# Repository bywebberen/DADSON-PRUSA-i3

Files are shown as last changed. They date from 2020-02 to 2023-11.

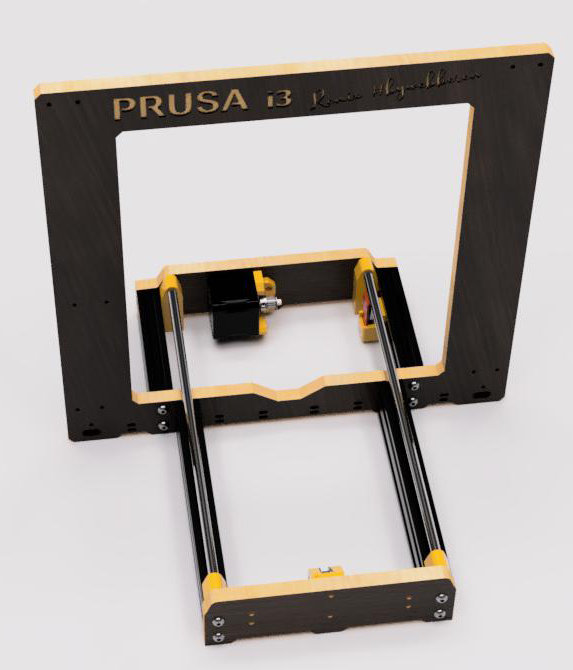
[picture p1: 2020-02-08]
IMGs/DADSON_Prusa_i3_printer_Y_AXIS.jpg

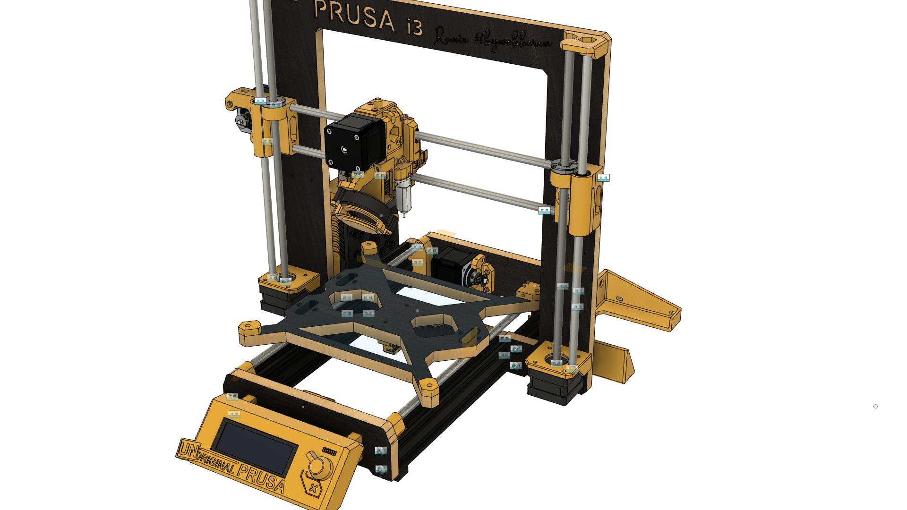
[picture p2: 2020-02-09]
IMGs/DADSON Prusa i3 printer v220.jpg

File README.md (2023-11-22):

# DADSON-PRUSA-i3
Another clone of the amazing PRUSA i3 3D-Printer by Josef Prusa

If you found this useful, please donate what you think it is worth to my paypal.me. Help cover the time of design.
Thanks, Enjoy!
http://www.paypal.me/bywebberen

Update 22.11.2023 - Added in an extruder assembly for the X1C bambulab hotend clone or real (remember this heater is running 24 volt)

Update 10.09.2020 — The Clip-on piece was actually uploaded...! Find it in X-axis folder named: "Homing_Block_sensorless homing.stl"

Update 29.08.2020 — There is a new motor piece for the X-axis part, if you haven't already printed it?
I will make a clipon piece today, which will  work the same. It is for when homing, if you are above the stability piece on the Z-axis, you will get 2 different homes for x-axis - this is of course only when using the sensorless homing version.

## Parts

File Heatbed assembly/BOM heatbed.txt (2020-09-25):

1	Heated bed (with wires)
4	M3 by 25mm bolts
4	M3 selflocking nuts
4	M3 washers
4	Aluminium spacers 6mm
1	Cable restraint
	(printed part)
1	50cm 3mm nylonfilament
3	Zip ties

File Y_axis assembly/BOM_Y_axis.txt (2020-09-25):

First Part of assembly
pcs.	Description.
1 	Main wood frame
2 	2040 vslot extrusions 205mm
2 	2040 vslot extrusions 120mm
8 	M5 by 25mm bolts
8 	M5 by 20mm bolts
3 	LM8UU Bearings
2 	8mm by 330mm steelrods
4 	Rodmounts printed part
10 	Slide-in Tnuts
1	Backplate wood
1	Frontplate wood
2 	Stabilizers printed part
4 	M5 by 8mm low profile bolts
4 	3.5mm woodscrews buttonhead
3 	M3 self locking hexnuts
1 	Idlermount printed part
1 	GT2 idler pulley
1 	M3 by 20mm bolt
2  	M3 hexnuts
1 	Motormount printed part
1 	Nema17 stepper motor
2 	M3 by 10mm bolts
1 	16 teeth GT2 pulley
4 	M3 by 18mm bolts
4 	M3 washers
3 	LM8UU nests printed part
6 	M3 squarenuts
3 	Nests-securer printed part
6 	M3 by 10mm bolts
1 	Bedmount wood piece
1 	Beltmount printed part
1 	GT2 belt
2 	M3 by 25mm bolts
2 	M3 washers
4	Rubberfeets(NinjaFlex)

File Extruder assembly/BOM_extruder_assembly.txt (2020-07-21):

Extruder assembly			
Pcs	Description				Type
1	Extruder-idler				Printed part
1	Bondtech-Style pulley(no hole)		*Hardware
2	Pulley needle bearing			*Hardware
1	Pulley shaft				*Hardware
2	M3 Snuts/squarenuts			Hardware
1	Extruder body				Printed part
2	M3 hexnuts				Hardware
	(no filament sensor on the DADSON
	but you still need to do step 7 [2 times M3 hexnuts])
1	M3 by 30mm bolt				Hardware
2	M3 Washers				Hardware
1	M3 Hexnut (temporarily use)		Hardware
1	Nema17 Steppermotor			Hardware
1	Bondtech-Style pulley(with hole)	*Hardware
	* Buy it as a set online "Bondtech dual gear drive"
2	M3 by 30mm bolts			Hardware
1	Piece of 1.75mm filament for alignment	Filament
2	M3 by 40mm bolts			Hardware
2	Extruder springs (5x20x1mm)		Hardware
1	Extruder-cover				Printed part
3	M3 Snuts/squarenuts			Hardware
2	M3 by 25mm bolts			Hardware
1	SpiderHotend assembled with heat+Therm.	Hardware
	(Hotend is same style as CR10 printer)
1	45mm PTFE tube (capricorn)		Hardware
2	M3 by 20mm bolts			Hardware
2	M3 hexnuts				Hardware
4	M3 by 15mm bolts			Hardware
1	40mm Hotend fan 12v			Hardware
1	Radial-fan for partcooling		Hardware
1	Nozzlefan-45deg-support			Printed part
1	Nozzlefan (in ASA filament, for heat)	Printed part
1	M3 by 25mm bolt				Hardware
2	M3 by 10mm bolts			Hardware
2	M3 Hexnut				Hardware
1	Induction sensor (12mm width)		Hardware
1	M3 by 15mm(18mm will do fine)		Hardware
1	M3 Snuts/squarenuts			Hardware
1	M3 by 40mm bolts			Hardware
1	M3 by 30mm bolts			Hardware
1	M3 by 18mm bolts			Hardware
1	500mm by 3mm NylonFilament		Filament
1	X-carriage-back				Printed part
1	Cable-holder				Printed part
1	M3 hexnut				Hardware
1	M3 by 10mm bolt	(temporarily use)	Hardware
1	M3 by 40mm bolt				Hardware
5	M3 by 10mm bolts			Hardware
1	Cable restrain				Printed part
2	M3 by 20mm bolts			Hardware
2	M3 washers				Hardware
2	M3 hexnuts				Hardware
1	Filament-sensor-cover			Printed part
1	PTFE tube 13mm lenght			Hardware
2	M3 by 10mm bolts			Hardware
1	Idler-plug				Printed part
(the last of the parts will be used in a later video)
1	Textile Sleeve (>> 500mm)		Hardware
5	Zip-Ties				Hardware
	Additional zip-ties			Hardware

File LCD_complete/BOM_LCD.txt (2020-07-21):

LCD assembly Bill Of Materials

Pcs Description             Type
1   LCD screen              Eletcronics
2   LCD cables (EXP1+EXP2)  Electronics
1   LCD cover               Printed part
1   LCD knob                Printed part
2   LCD support             Printed part
4   M3 by 20mm bolts        Hardware
4   M3 Squarenuts           Hardware
4-6 ClipForLCDwires         Printed part
2   M3 by 10mm              Hardware

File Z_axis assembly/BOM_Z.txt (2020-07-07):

Bill Of Materials

pcs.      Description                                   Type
1         Z-axis-bottom-left                            Printed part
1         Z-axis-bottom-right                           Printed part
6         M3 by 20mm bolt                               Hardware
6         M3 Washers                                    Hardware
6         M3 Hexnuts (preferable selflocking)           Hardware
2         Nema17 steppermottors w/ leadscrew 320mm      Hardware
2         Leadscrew brassnuts                           Hardware
2         Nema17 "ConeTop" pieces                       Printed part
8         M3 by 10mm                                    Hardware
2         Leadscrew/brassnut adaptors                   Printed part
4         M3 Hexnuts                                    Hardware
4         M3 by 10mm                                    Hardware
4         M3 by 15mm "buttonhead/low profile" bolts     Hardware
4         M3 Squarenuts/Snuts                           Hardware
2         8mm by 320mm steelrods                        Hardware 
1         Z-axis-top-left                               Printed part
1         Z-axis-top-right                              Printed part
4         M3 by 20mm bolts                              Hardware
4         M3 Washers                                    Hardware
4         M3 Hexnuts (preferable selflocking)           Hardware
-         GT2 timingbelt                                Hardware

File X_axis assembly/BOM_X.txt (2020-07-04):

BILL OF MATERIAL (By order of usage)
Pcs   Description             Type
1     X-end motormount        Printed part
1     X-end idlermount        Printed part
4     LM8UU linear bearings   Hardware
1     M3 by 18mm bolt         Hardware
1     M3 Nylocnut             Hardware
1     Idler for GT2 belt      Hardware
1     M3 S-nut/squarenut      Hardware
1     M3 by 18mm bolt         Hardware
2     8mm by 370mm steelrod   Hardware
3     LM8UU linear bearings   Hardware
1     NEMA17 steppermotor     Hardware
1     16T GT2-pulley          Hardware
3     M3 by 18mm bolts        Hardware
1     X-carriage              Printed part
5     M3 S-nut/squarenut      Hardware
2     Zip-Ties                Hardware

You should be able to just follow the original Prusa MK3 manual for this

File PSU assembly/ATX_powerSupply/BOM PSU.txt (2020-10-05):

pcs.    Description                     Type
1       ATX powersupply                 Electronic
4-5     M5 by 8mm low-profile bolts     Hardware
1       PSU mount1                      Printed part
1       PSU mount2                      Printed part

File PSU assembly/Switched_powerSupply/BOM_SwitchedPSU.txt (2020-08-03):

Bill Of Material for the switched PSU version

pcs     Description                                                                                     Type
1       Switched "LED" powersupply                                                                      Electronics
1       10A 250V 3Pin IEC320 C14 Inlet Module Plug Fuse With Switch Male Power Socket                   Electronics
1       Main_PSU_mount                                                                                  Printed part
1       Main_PSU_lid                                                                                    Printed part
1       1224VoltOut                                                                                     Printed part
2       2040_PSU_anchor_(A+B)                                                                           Printed part
4       M5 by 20mm low-profile bolts                                                                    Hardware
2-6     M4 by 10mm bolts                                                                                Hardware
2       M3 Hexnuts                                                                                      Hardware
2       M3 by 30mm bolts                                                                                Hardware

(Optional - for extra top mounting in 2040 extrusion)
2M5 by 8mm low-profile bolts                                                                            Hardware
2M5 Drop-in T-nuts                                                                                      Hardware

Wires to connect 230v to PSU + wires for secondary 12/24volt out

10A 250V 3Pin IEC320 C14 Inlet Module Plug Fuse With Switch Male Power Socket:
https://www.banggood.com/1pcs-10A-250V-3Pin-IEC320-C14-Inlet-Module-Plug-Fuse-With-Switch-Male-Power-Socket-p-1120059.html?ID=228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

Switched "LED" powersupply: (Example)
https://www.banggood.com/Wholesale-Switching-Power-Supply-Driver-AC-110V-or-220V-To-DC-12V-30A-360W-Transformer-for-LED-Strip-Light-p-39987.html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

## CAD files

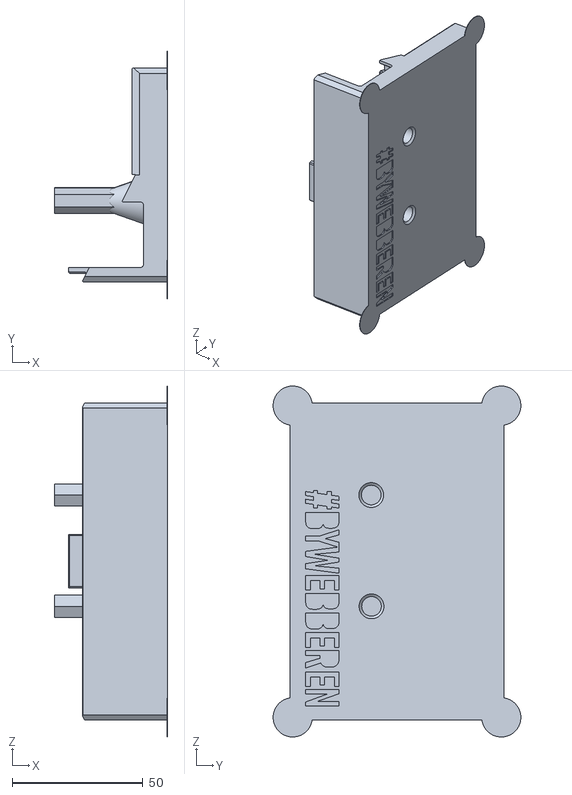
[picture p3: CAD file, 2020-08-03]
PSU assembly/Switched_powerSupply/Main_PSU_lid.stl
43.3 x 94.8 x 134.3

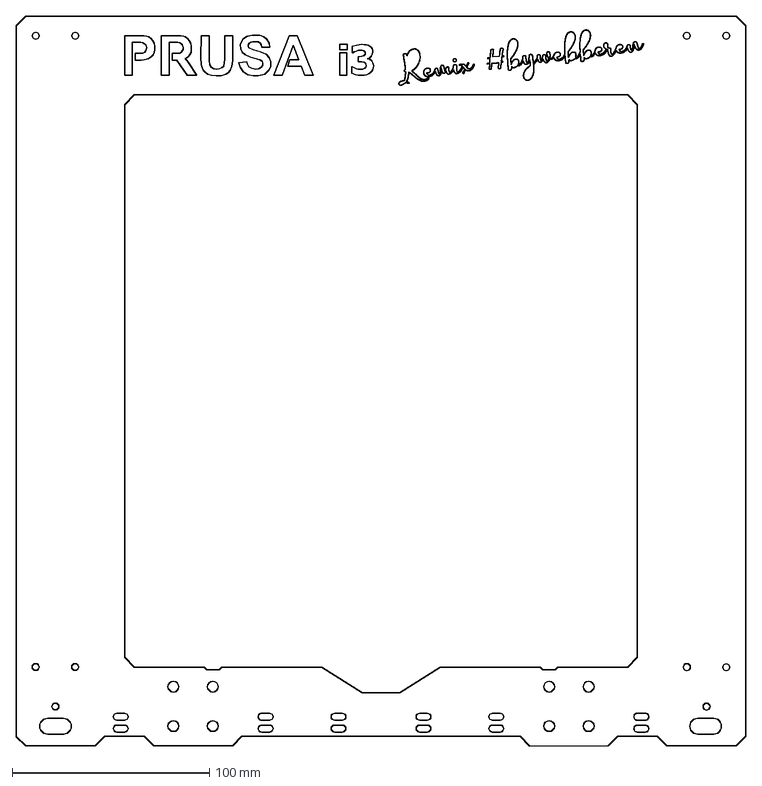
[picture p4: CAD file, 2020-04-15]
DXFs/MainFrame.dxf
370.0 x 370.0 mm

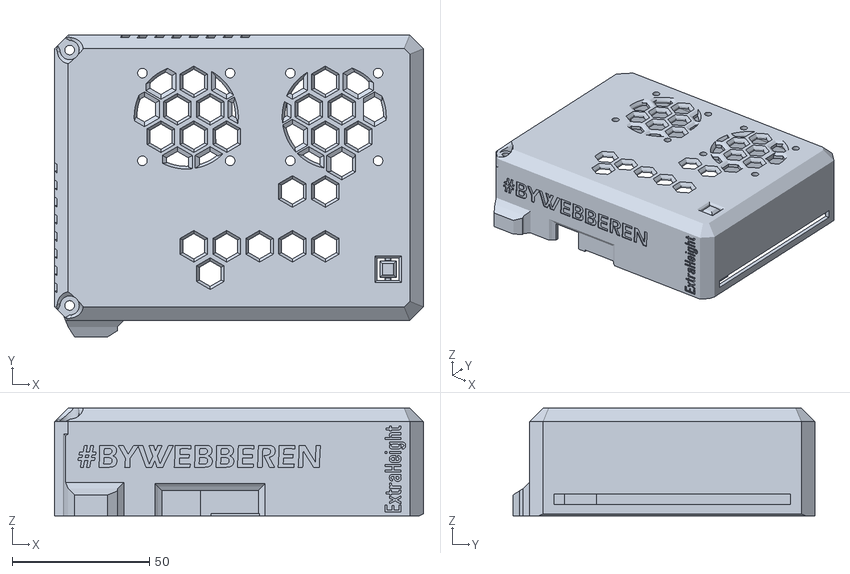
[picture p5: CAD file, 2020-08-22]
Bigtreetech SKR v1.3 Box/SKR_Top_extraHeightTMC2209.stl
134.7 x 110.3 x 39.4

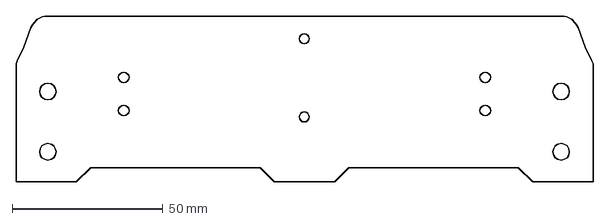
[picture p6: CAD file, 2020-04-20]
DXFs/Front_plate.dxf
191.6 x 55.0 mm

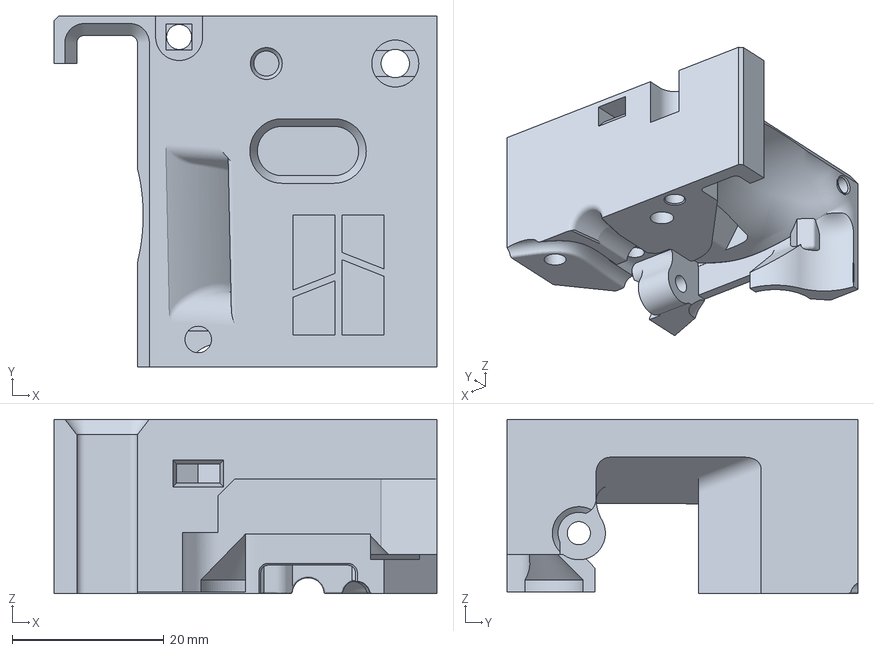
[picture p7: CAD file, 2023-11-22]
Extruder assembly/Extruder Cover_X1C_INDUCTIVE.3mf
50.5 x 46.2 x 23.0 mm

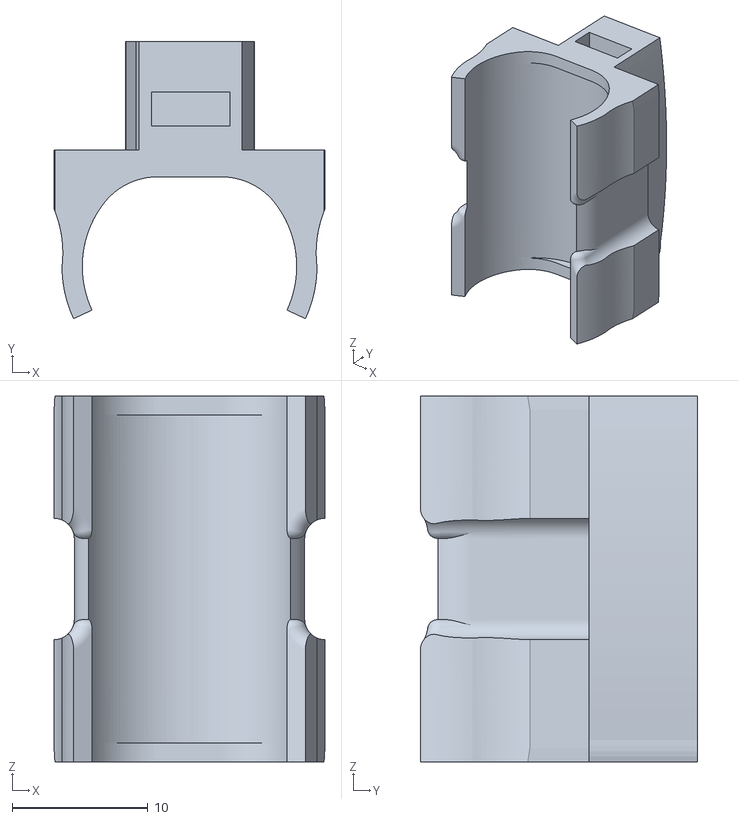
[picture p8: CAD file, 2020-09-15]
Heatbed assembly/LM8UU_nest_bed_V3.stl
20.0 x 20.5 x 27.0

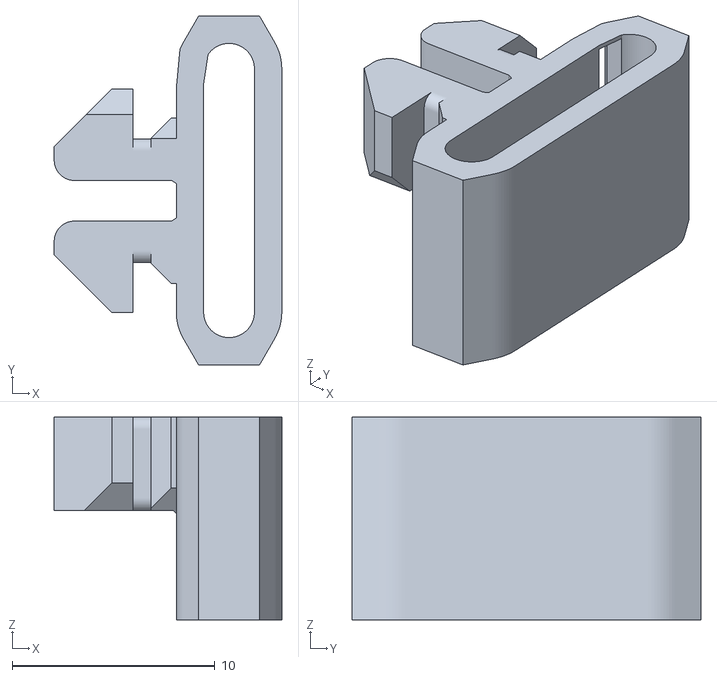
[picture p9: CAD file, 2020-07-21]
LCD_complete/ClipForLCDwires.stl
11.2 x 17.2 x 10.0

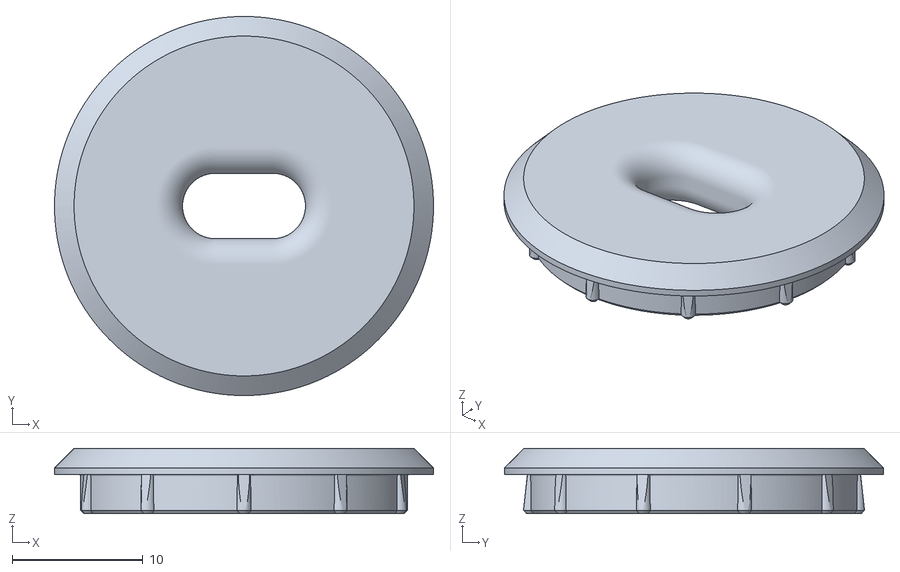
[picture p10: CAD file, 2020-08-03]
PSU assembly/ATX_powerSupply/ATX_PLUG.stl
29.0 x 29.0 x 5.00

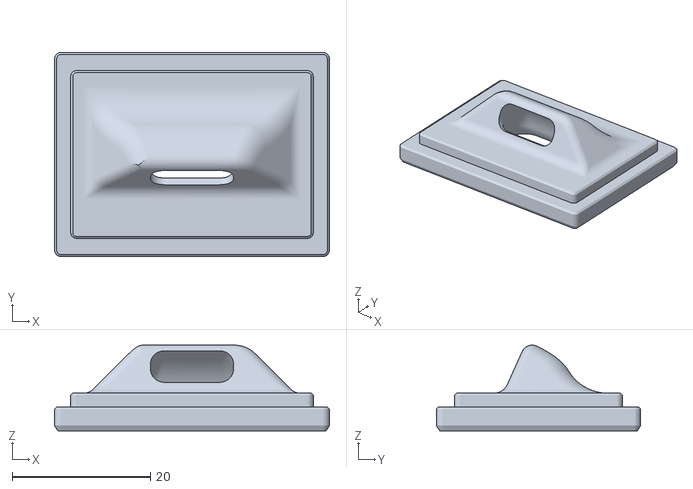
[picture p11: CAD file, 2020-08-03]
PSU assembly/Switched_powerSupply/1224VoltOut.stl
39.8 x 29.6 x 12.4

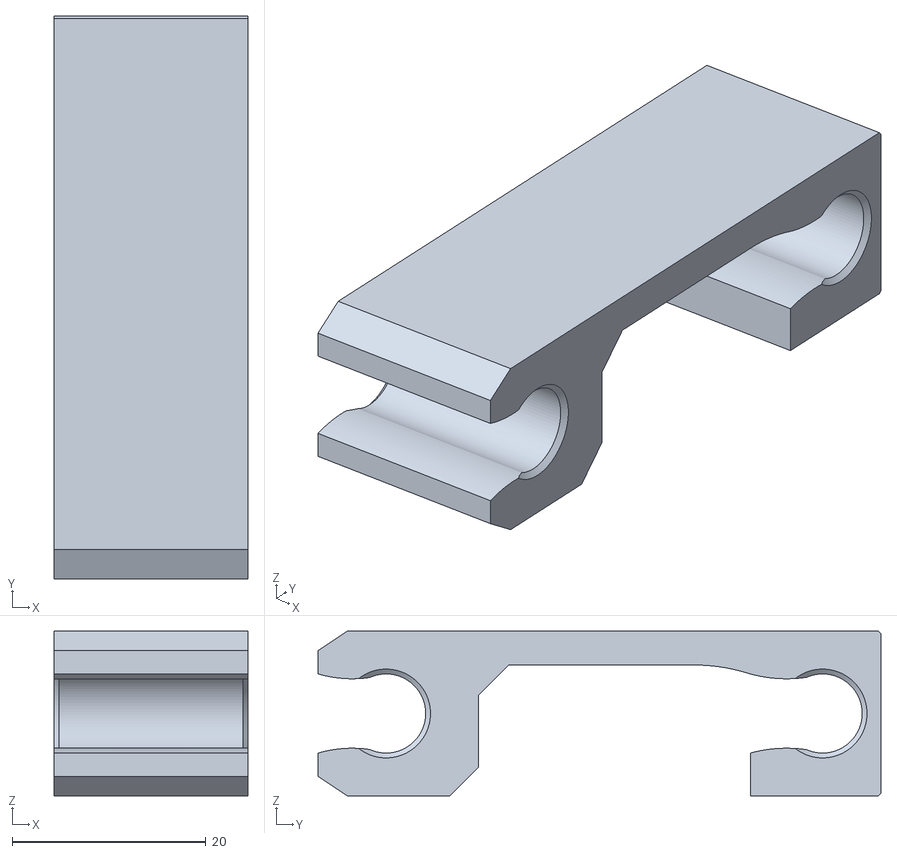
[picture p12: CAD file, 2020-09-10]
X_axis assembly/Homing_Block_sensorless homing.stl
20.0 x 58.0 x 17.0

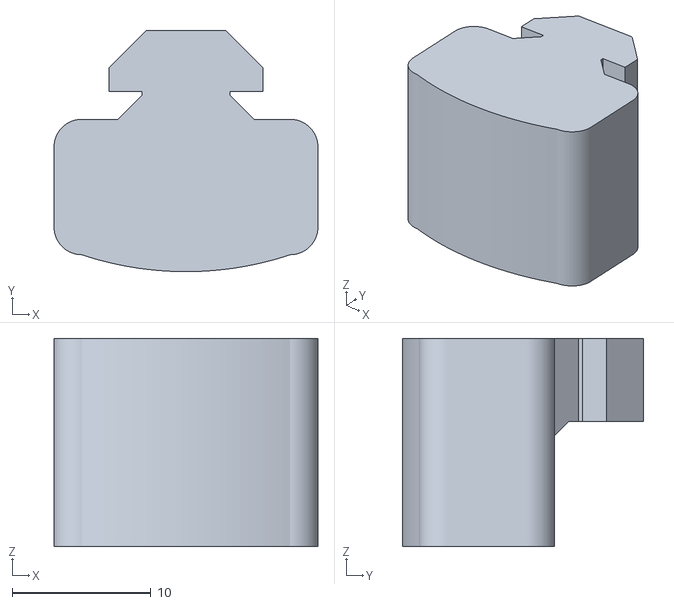
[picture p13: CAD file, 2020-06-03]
Y_axis assembly/RubberFeet_FLEXIBLE_v3_0520.stl
19.0 x 17.4 x 15.0

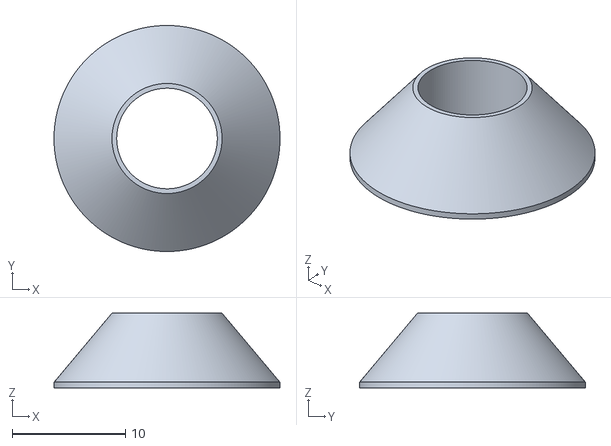
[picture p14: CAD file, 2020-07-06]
Z_axis assembly/Nema17TopShim v1.stl
20.0 x 20.0 x 6.61

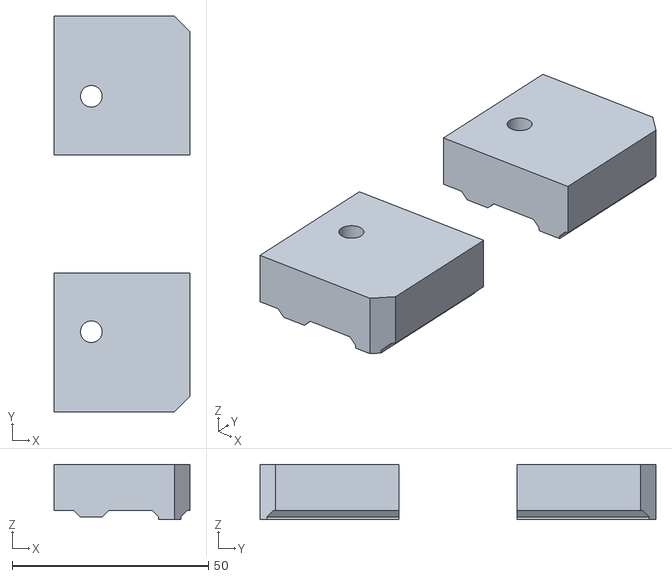
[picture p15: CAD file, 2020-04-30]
Bigtreetech SKR v1.3 Box/V-Slot_SpacersSKR_BOX.stl
34.6 x 100.9 x 14.0

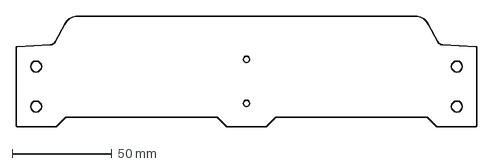
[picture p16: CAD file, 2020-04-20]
DXFs/Back_plate.dxf
230.4 x 55.0 mm

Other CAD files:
Extruder assembly/Extruder body_X1C_INDUCTIVE.3mf
Heatbed assembly/FastenerNestsBed.stl
LCD_complete/LCD Knob.stl
PSU assembly/ATX_powerSupply/PSU mount1.stl
Bigtreetech SKR v1.3 Box/SKR_Bottom_DADSON_VERSION.stl
Bigtreetech SKR v1.3 Box/SKR_Top_DADSON_VERSION.stl
DXFs/BedMount.dxf
Extruder assembly/Cable Holder.stl
Extruder assembly/DADSON Prusa i3 printer_Nozzle Fan_V5Wide v3.3mf
Extruder assembly/Extruder Body_E3D_V6.stl
Extruder assembly/Extruder Cover_E3D_V6.stl
Extruder assembly/Extruder Cover_SpiderHotend.stl
Extruder assembly/Extruder Cover_SpiderHotend_INDUCTIVE.3mf
Extruder assembly/Extruder Idler Plug.stl
Extruder assembly/Extruder Idler.stl
Extruder assembly/Extruder body_SpiderHotend.stl
Extruder assembly/Extruder body_SpiderHotend_INDUCTIVE.3mf
Extruder assembly/Filament Sensor Cover.stl
Extruder assembly/InletPartFan.stl
Extruder assembly/Nozzle Fan Holder.3mf
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

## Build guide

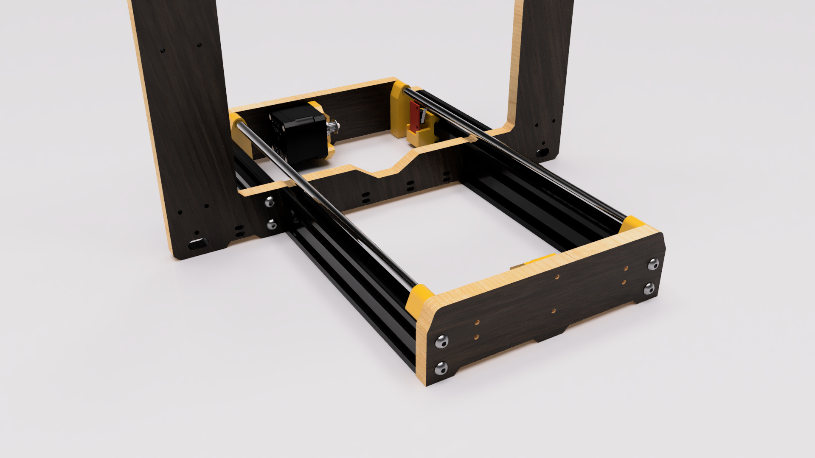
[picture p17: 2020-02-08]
IMGs/DADSON_Prusa_i3_printer_2020-Feb-08_07-20-16AM-000_CustomizedView1629463545_jpg.jpg

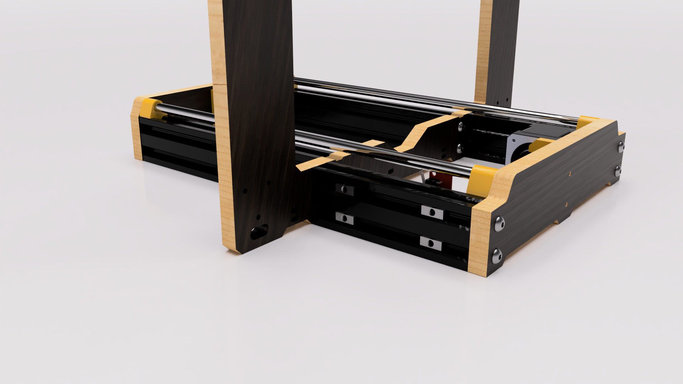
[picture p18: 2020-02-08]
IMGs/DADSON_Prusa_i3_printer_2020-Feb-08_07-32-34AM-000_CustomizedView1213494887_jpg.jpg

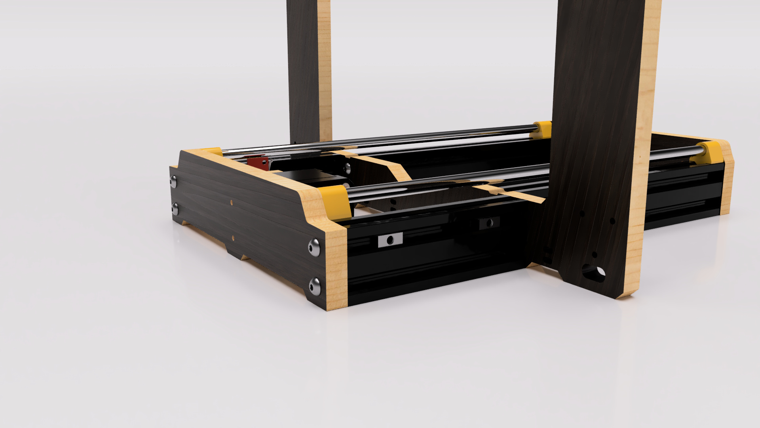
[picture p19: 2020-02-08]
IMGs/DADSON_Prusa_i3_printer_2020-Feb-08_07-33-05AM-000_CustomizedView8033316839_jpg.jpg

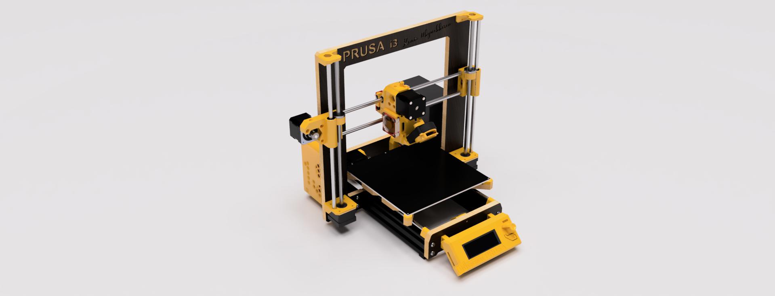
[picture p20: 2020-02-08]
IMGs/DADSON_Prusa_i3_printer_2020-Jan-11_09-11-38AM-000_CustomizedView13987289884.jpg

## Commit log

2020-02-08 Add files via upload
    The box for the SKR v1.3 and the MKS Gen L
    [SKR_Bottom_DADSON_VERSION.stl, SKR_Top_DADSON_VERSION.stl, V-Slot_SpacersSKR_BOX.stl]
2020-02-08 Create Link To original PRUSA assembly manual
    Use this guide as much as your own logical sense :)
2020-04-06 NEW version riser,
    with hole for 10x6mm aluminium spacer
    [NEW_BedRiser_restraint.stl]
2020-04-06 Update BOM heatbed.txt
2020-04-20 Add files via upload
    Some of the holes was the wrong size...
    [Back_plate.dxf, Front_plate.dxf]
2020-04-30 Just some minor tweaks
    [LCD Cover unORIGINAL MK3.stl, LCD Knob.stl]
2020-04-30 Slimmed the design
    [RodMountPiece_BackLeft.stl, RodMountPiece_BackRight.stl, RodMountPiece_FrontLeft.stl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]
2020-04-30 Some measurements where off after the "mirroring".
    [X-end Idler_Mirrored.stl, X-end Motor_mirrored_ENDSTOP.stl, X-end Motor_mirrored_STD.stl]
2020-04-30 Made them thicker for better room X-axis
    [V-Slot_SpacersSKR_BOX.stl]
2020-05-15 Uploaded stabilizers for Z axis.
    Yo will need 4 M5 low profile bolts and 4 drop in t-nuts
    Also you need the thicker spacers for the mainboard case
    [Stabilizer_PSULeft.stl, Stabilizer_PSUright.stl]
2020-06-03 this is the correct thickness of 6mm
    [NEW_BedRiser_restraint.stl]
2020-06-03 More Stable flexibleFeets
    These can be installed afterwards
    [RubberFeet_FLEXIBLE_v3_0520.stl]
2020-06-05 Add files via upload
    Made further tighten function to remove the need for zipTies
    [LM8UU_nest_bed_V2.stl]
2020-07-03 ConeTop for NEMA17
    Designed the dust and filament repelling toppiece for the z-axis NEMA17 stepperdrivers shaft
    [Nema17TopShim v1.stl]
2020-07-04 Update BOM_X.txt
    Made the BOM-list while building for correct allocation of parts
2020-07-04 Update BOM_X.txt
    Updated the BOM-list while building for correct parts allocation.
2020-07-06 The dimensions where a bit off
    New release with better printability and larger hole for the leadscrew
    [Nema17TopShim v1.stl]
2020-07-20 Added BOM for LCD assembly
2020-07-21 V-slot clip for wires like 2xLCD cables
    [ClipForLCDwires.stl]
2020-08-03 Update BOM PSU.txt
2020-08-05 Added Extruder BODY and COVER for E3D V6 hotends
    [Extruder Body_E3D_V6.stl, Extruder Cover_E3D_V6.stl]
2020-08-10 Small changes made to the piece
    [PSU mount2.stl]
2020-08-22 New File uploaded
    Extra height TOP-PIECE for the higher heatsink on for instance TMC 2209's
    [SKR_Top_extraHeightTMC2209.stl]
2023-01-01 For the SPIDERhotend or CR10 style hotend
    There was some changes made to the holder for the inductive probemount
    [Extruder Cover_SpiderHotend_INDUCTIVE.3mf, Extruder body_SpiderHotend_INDUCTIVE.3mf]
2023-01-02 New versions
    These files are better suited for long time use. The probemount is heavier - to prevent it from sacking.
    [Extruder Cover_SpiderHotend_INDUCTIVE.3mf, Extruder body_SpiderHotend_INDUCTIVE.3mf]
2023-11-22 Update README.md
    New updates to the Extruder versions
